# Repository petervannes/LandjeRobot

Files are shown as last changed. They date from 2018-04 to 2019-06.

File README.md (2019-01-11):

# Landje Robot

cover

Welcome to the Landje Robot repository. Landje Robot is an fully open source STEM robot and named after the elementary school of my kids where i started teaching programming using this robot. It is a common object avoidance and line following robot like many others. Landje Robot deviates in two aspects from many other builds.

First, Landje Robot is fully documented. There is a [Preparation guide](https://petervannes.github.io/LandjeRobot/Landje%20robot%20Kit%20preparation.html) which describes the bill of material, assembly of wire looms and other main parts and designs of the 3D printed parts. Next to the [Preparation guide](https://petervannes.github.io/LandjeRobot/Landje%20robot%20Kit%20preparation.html) there is a [Student guide](https://petervannes.github.io/LandjeRobot/Student%20guide%20ENU.html) with programming lessons in [English](https://petervannes.github.io/LandjeRobot/Student%20guide%20ENU.html) and [Dutch](https://petervannes.github.io/LandjeRobot/Student%20guide%20NLD.html).

Secondly, Landje Robot has its own instruction set. The instruction set is also documented in [Dutch](https://petervannes.github.io/LandjeRobot/instructionset%20NLD.html) and [English](https://petervannes.github.io/LandjeRobot/instructionset%20ENU.html). This instructionset simplifies the control of the sensors, motors, led and switch. With this instruction set and robot i made an attempt to create instruction material for kids who have overgrown the level of programming in Scratch or similar languages like Blockly and Alice. Programming in Scratch is a good starting point to grab the concepts of programming, but it has it's limitiations. (as this robot has it's own)

Switching from the safe Scratch language to C is challenging with it syntax and runtime errors. Therefore the complexity of controlling the I/O ports to read sensor data or control the servo- and stepper motors is delegated to the provide instructionset. Moving the robot forward is now reduced to a `move ( direction )` instruction.

For documentation and components there has been made use of open source components and products as much as possible. Documentation is written in MarkDown or HTML format. Graphical content is made using [GIMP](https://www.gimp.org) for bitmaps and [Inkscape](https://inkscape.org/en/) for vector oriented images.

All documentation is clearly published [here](https://petervannes.github.io/LandjeRobot/)

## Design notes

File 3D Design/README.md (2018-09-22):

# Landje ROBOT 3D Printer Parts

The Landje robot is made up of various 3d printed parts.
You can download the stl-files for the different parts directly from the [LandjeRobot](https://github.com/petervannes/LandjeRobot/tree/master/3D%20Design) GitHub repository.

The parts shown on the [blog](http://reddipped.com) or in the guides are printed on a Ultimaker 3 using original Ultimaker PLA and PVA filament for best results. Optimal UM3 Profile settings for printing these parts are available in the folder [/3D Design/UM3](https://github.com/petervannes/LandjeRobot/tree/master/3D%20Design/UM3).

You can always change the model to your needs. The original design is available on [TinkerCad](https://www.tinkercad.com/things/dualnxm5zyQ-landje-robot).

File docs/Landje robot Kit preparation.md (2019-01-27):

# Landje robot Kit preparation

[TOC]

## Introduction

This guide documents the parts and tools to be purchased to create a complete Landje robot kit.
Part of the preparation is assembling the wiring looms and preparation of the led and its wiring.
If you have completed this guide the kit will reassemble the picture below. 



## Part list

### Hardware

|Qty|Article|Details|Est.&nbsp;&nbsp;price|
|:---|:---|:---|:--|
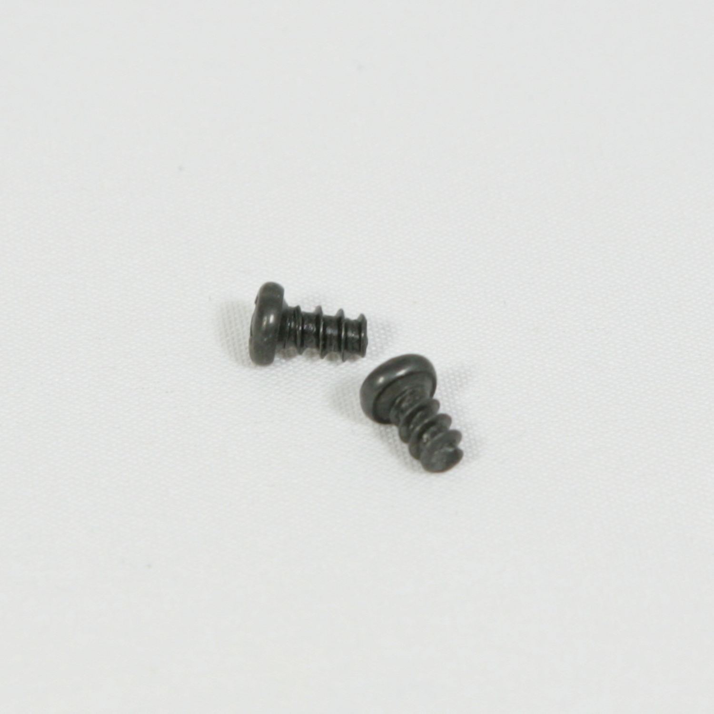
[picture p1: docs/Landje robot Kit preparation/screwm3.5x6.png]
|4| Philips head self-tapping micro screws. M3.5x6|[ AliExpress](https://nl.aliexpress.com/item/100Pcs-M2-6-M3-M3-5-M4-PB-Phillips-Head-Micro-Screws-Round-Head-Self-tapping/32818885586.html)|€ 0,13|
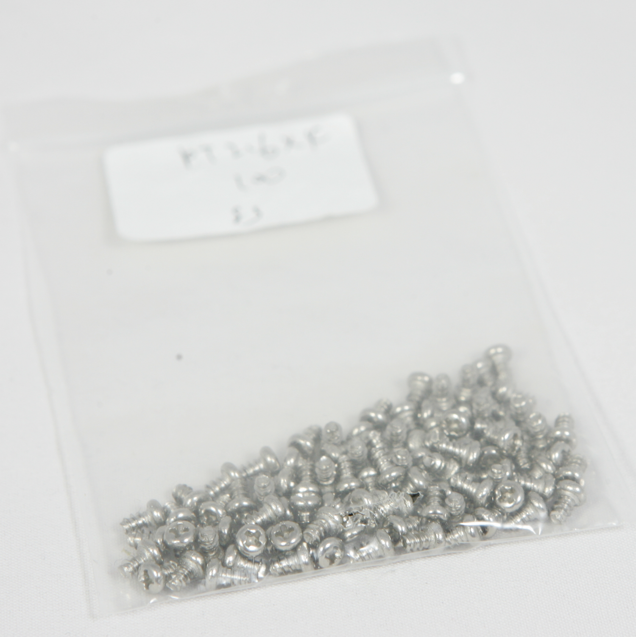
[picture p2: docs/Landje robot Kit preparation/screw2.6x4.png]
|10| Philips head self-tapping micro screws. M2.6x4 |  [AliExpress](https://nl.aliexpress.com/item/100pcs-lot-M2-M2-3-M2-6-M3-Stainless-steel-pan-head-philips-cut-off-tail/32811488462.html)|€ 0,28|
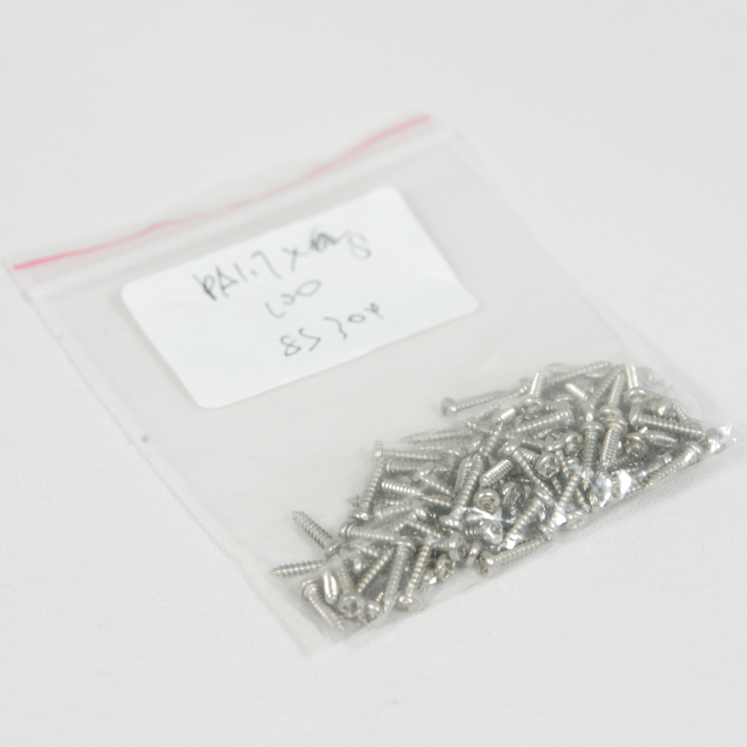
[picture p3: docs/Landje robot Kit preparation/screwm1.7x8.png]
|4| Philips head self-tapping micro screws. M1.7x8 |  [AliExpress](https://nl.aliexpress.com/item/100pcs-lot-M1-M1-2-M1-4-M1-5-M1-6-M1-7-Stainless-steel-phillips/32805873422.html)|€ 0,14|
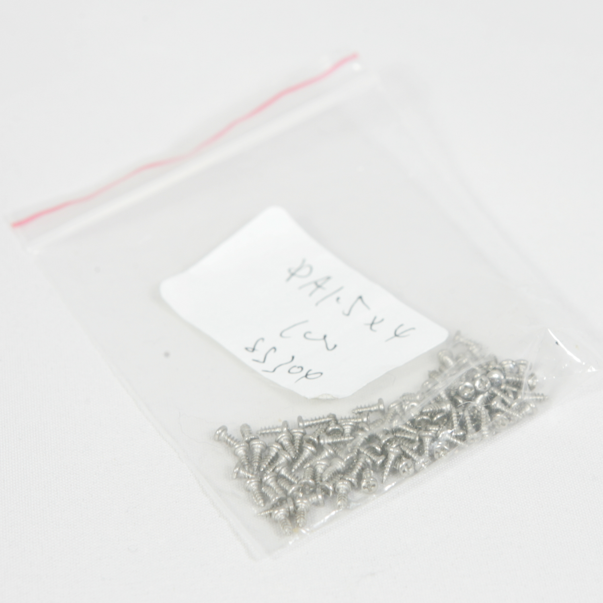
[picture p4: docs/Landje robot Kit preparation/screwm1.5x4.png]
|4| !!!!!!!!!!!!!!!! CORRECION Philips head self-tapping micro screws. M1.7x4 |  [AliExpress](https://nl.aliexpress.com/item/80pcs-M2-Phillips-head-micro-screws-round-head-self-tapping-electronic-small-screws-Black-zinc-Hard/32596628894.html)|€ 0,12|

### Electronics 

|Qty|Article|Details|Est.&nbsp;&nbsp;price|
|:---|:---|:---|-----:|
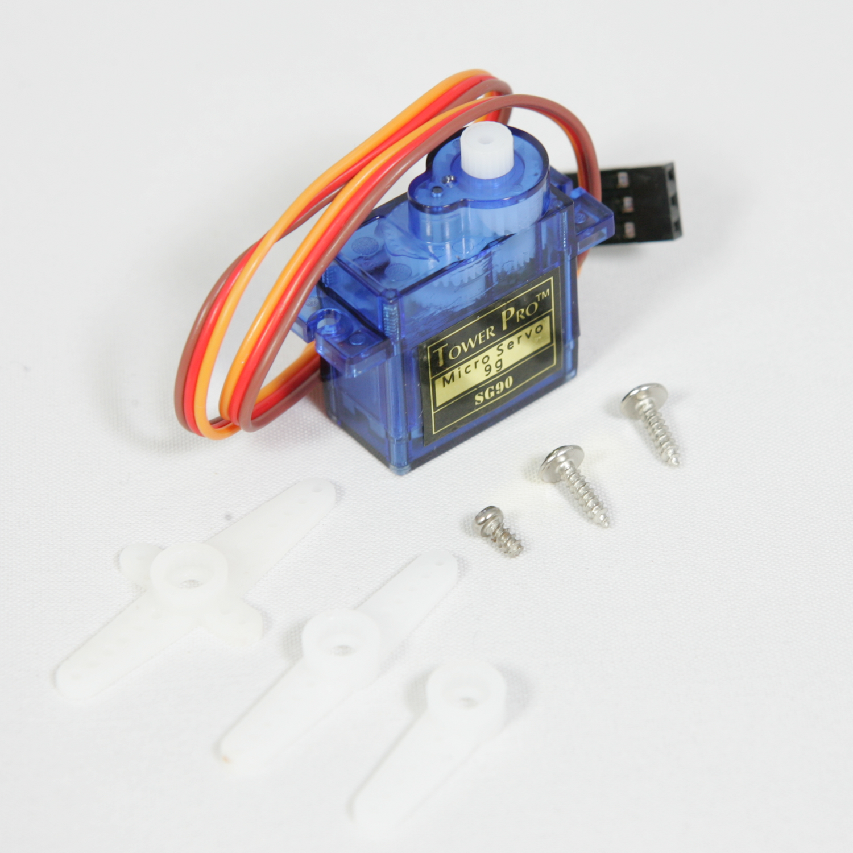
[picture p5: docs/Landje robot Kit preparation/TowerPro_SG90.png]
|1|Tower pro SG90 RC Micro Servo 9g |  [AliExpress](https://nl.aliexpress.com/wholesale?catId=0&initiative_id=SB_20171217044656&SearchText=sg90+micro+servo)|€ 1.05|
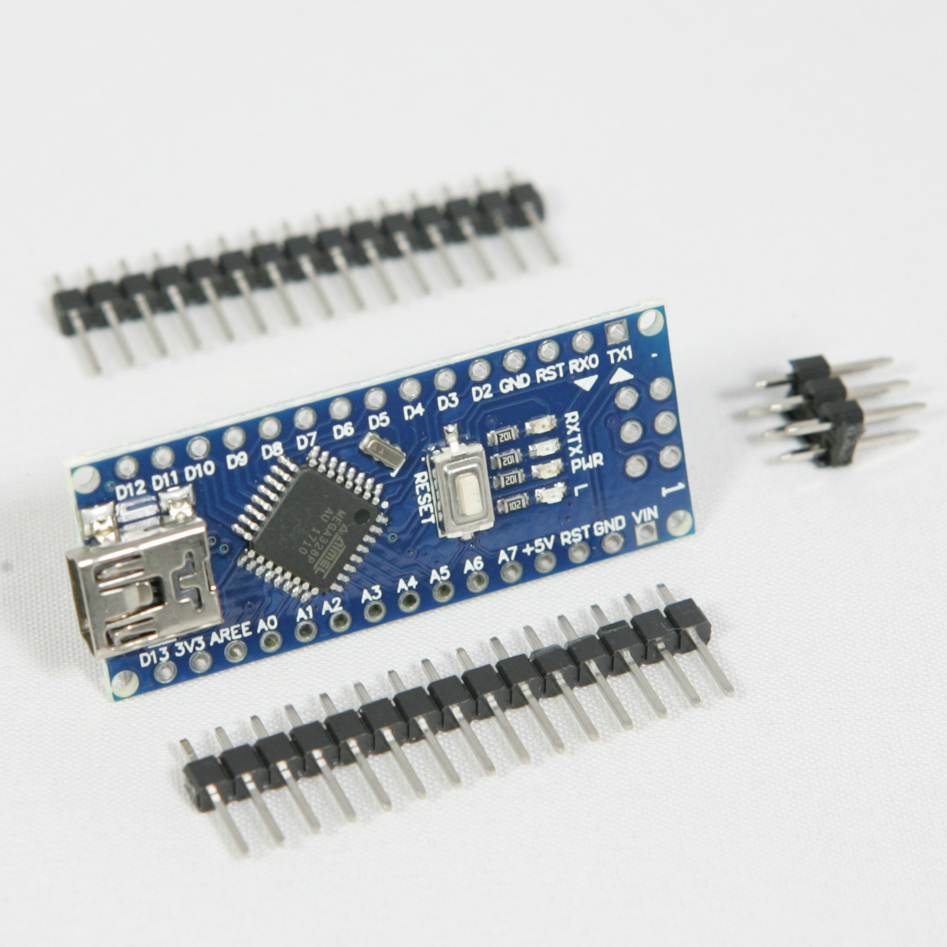
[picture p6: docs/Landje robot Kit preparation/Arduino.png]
|1|Arduino Nano 3.0</br> CH340 USB driver 16 Mhz|  [AliExpress](https://nl.aliexpress.com/w/wholesale-arduino-nano-ch340-usb-driver.html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)| € 2,00|
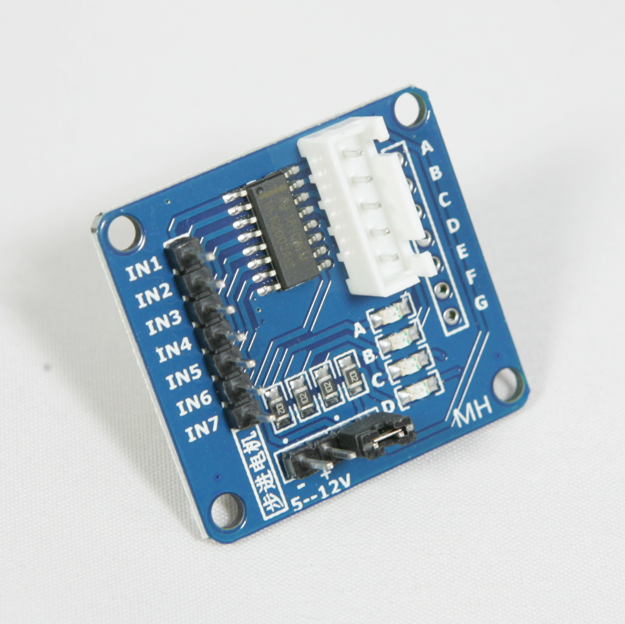
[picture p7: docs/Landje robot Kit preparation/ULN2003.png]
| 2 | ULN2003 Stepper Motor Driver Board SMD | [AliExpress](https://nl.aliexpress.com/item/High-power-ULN2003-Stepper-Motor-Driver-Board-Test-Module-For-Arduino-AVR-SMD/32561202872.html) | € 1,16 |
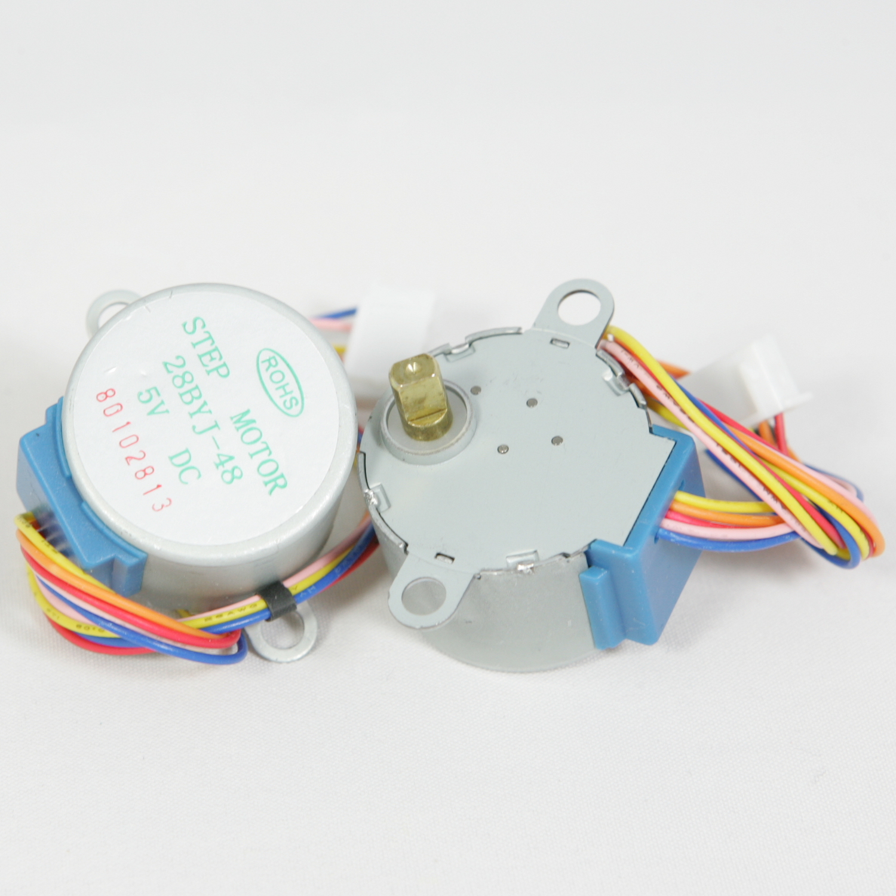
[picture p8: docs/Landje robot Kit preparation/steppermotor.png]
| 2 | 28BYJ-48-5V Stepper motors | [AliExpress](https://nl.aliexpress.com/item/LIXF-2017-HOT-New-38g-Silver-Plastic-28BYJ-48-5V-4-Phase-5-Wire-DC-5V/32827355981.html) | € 2,28 | 
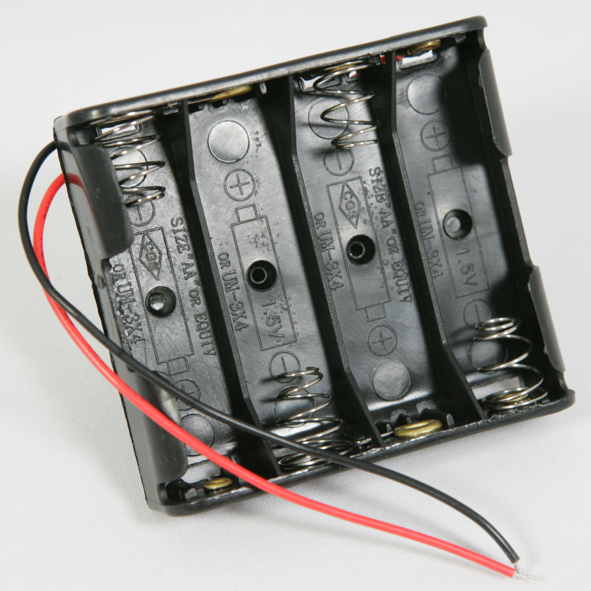
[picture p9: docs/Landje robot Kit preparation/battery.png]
| 1 | AA Power Battery Storage</br> Case Plastic Box Holder With 4 Slots | [AliExpress](https://nl.aliexpress.com/item/Top-Quality-Hot-Sale-1pcs-AA-Power-Battery-Storage-Case-Plastic-Box-Holder-With-4-Slots/32685809303.html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) | € 0,40|
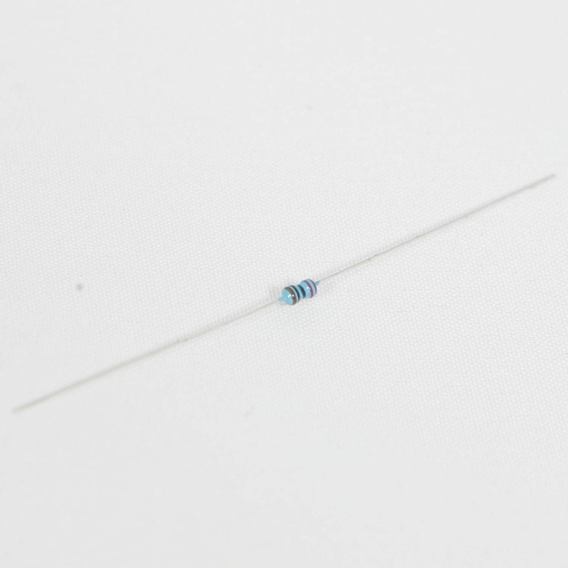
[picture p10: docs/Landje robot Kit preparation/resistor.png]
| 1 | 1/6W Metal Film Resistor 220Ω | [AliExpress](https://nl.aliexpress.com/item/100pcs-1-6W-Metal-Film-Resistor-220-ohm-220-R-1-Tolerance-Precision-RoHS-Lead-Free/1852424272.html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) | € 0,01 |
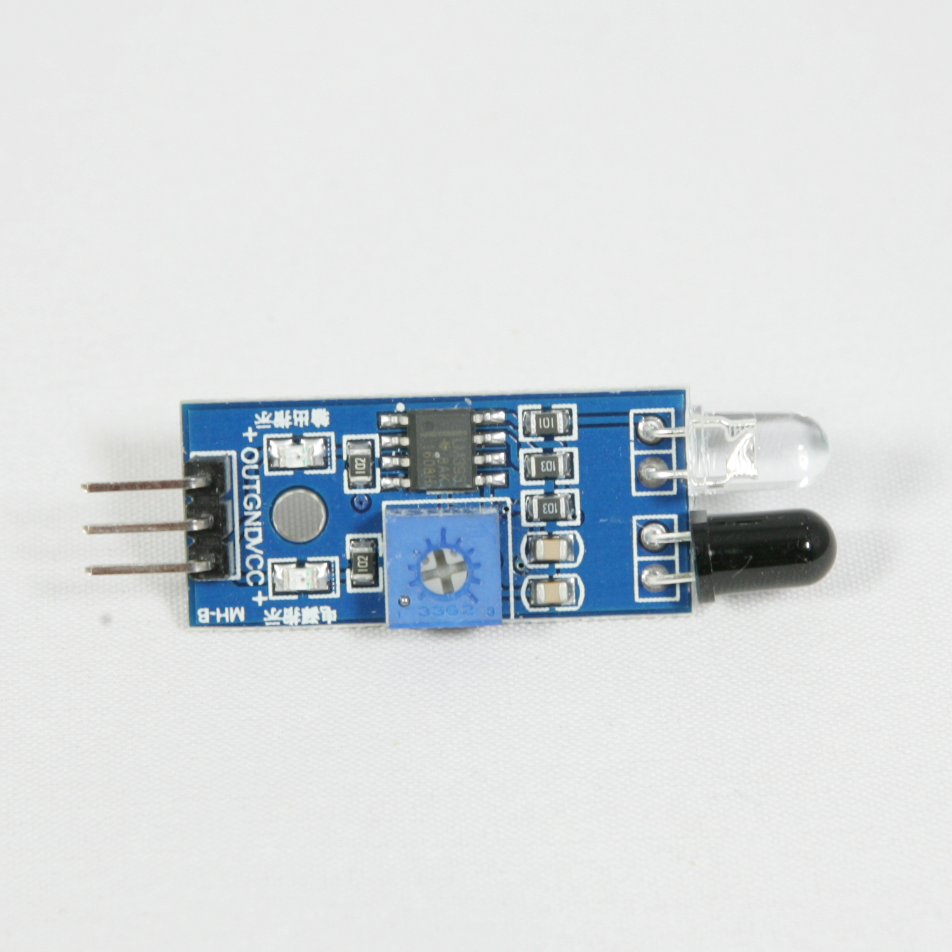
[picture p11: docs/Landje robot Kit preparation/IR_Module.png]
| 2 | IR Infrared Obstacle Avoidance Sensor Module | [AliExpress](https://nl.aliexpress.com/item/IR-Infrared-Obstacle-Avoidance-Sensor-Module-for-Arduino-Smart-Car-Robot-3-wire-Reflective-Photoelectric/32340011898.html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) | € 0,90 |
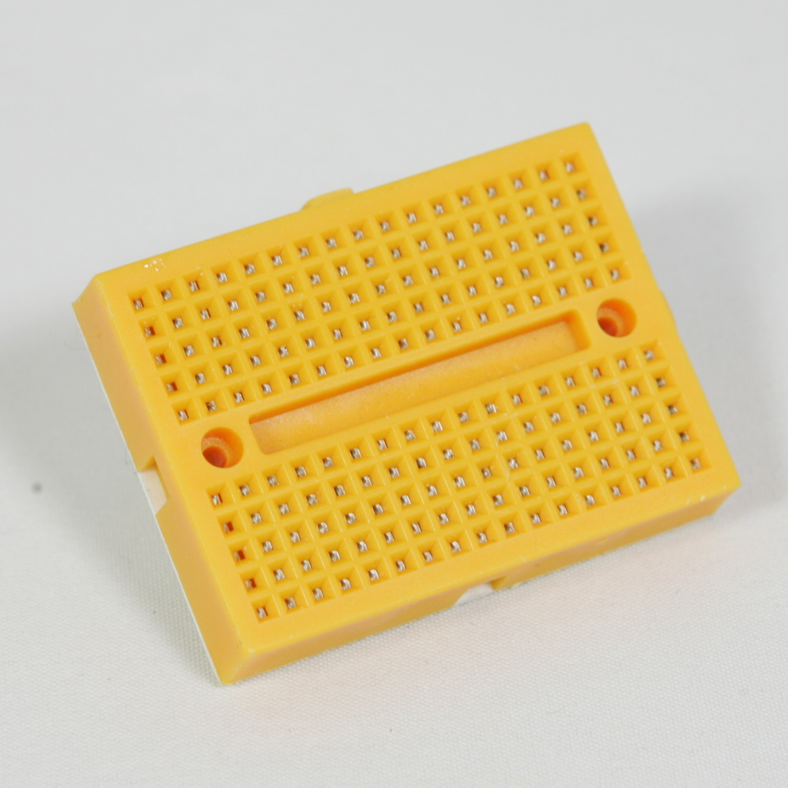
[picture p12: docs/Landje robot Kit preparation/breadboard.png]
| 1 | SYB-170 Mini Solderless Prototype Breadboard | [AliExpress](https://nl.aliexpress.com/item/3pcs-lot-170-Tie-points-Mini-Solderless-Prototype-Breadboard-for-ATMEGA-PIC-Arduino-UNO-Wholesale-Retail/1536996696.html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) | € 0,45 |
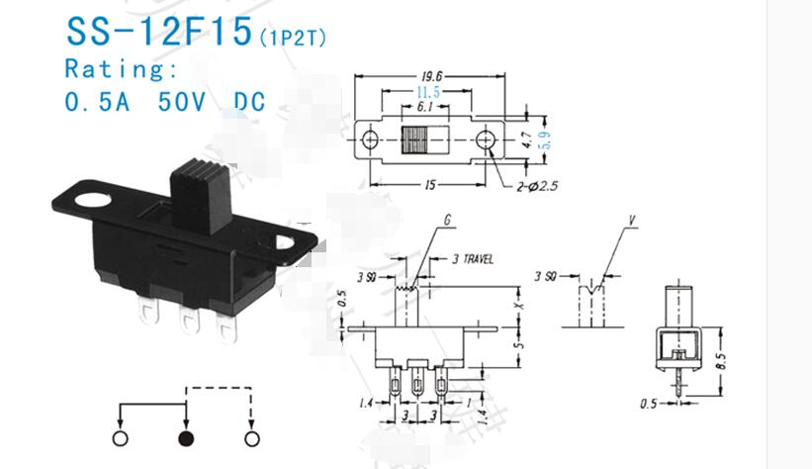
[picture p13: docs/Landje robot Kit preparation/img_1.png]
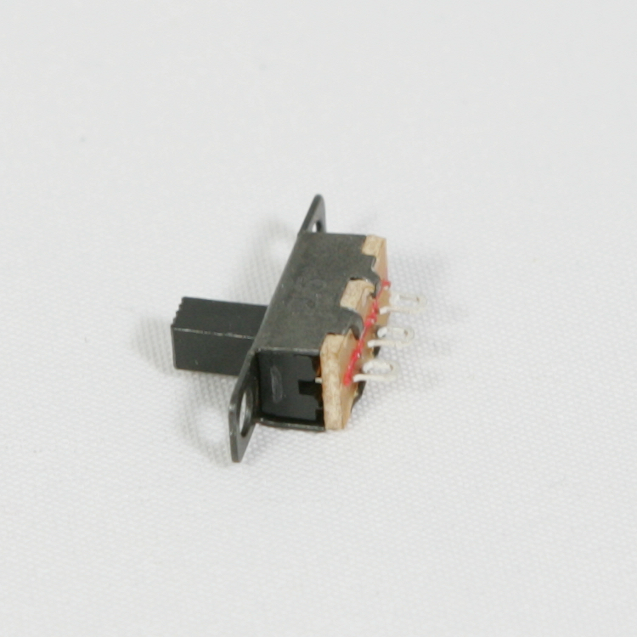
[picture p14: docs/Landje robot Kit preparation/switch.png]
| 2 | 5mm Height Knob 3 Pin 2 Position</br> 1P2T SPDT Panel Slide Switch 0.5A | </br>[AliExpress](https://nl.aliexpress.com/item/50-Pcs-5mm-Height-Knob-3-Pin-2-Position-1P2T-SPDT-Panel-Slide-Switch-0-5A/32706649448.html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) | € 0,16|
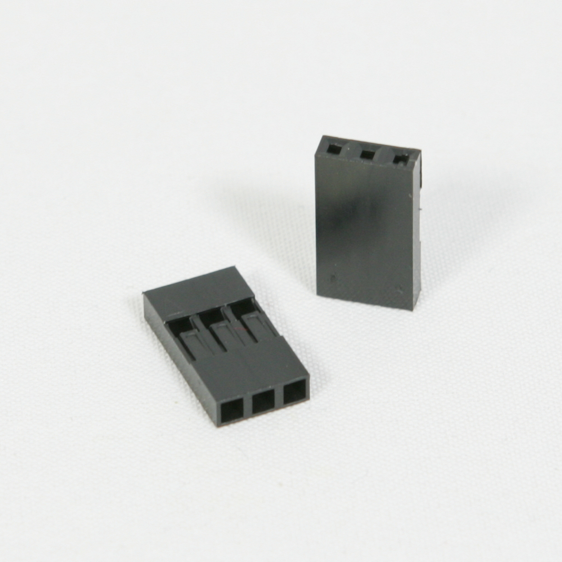
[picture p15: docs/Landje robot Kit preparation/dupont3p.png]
| 2 | Dupont connector 3 pin single row 2.54 mm | [AliExpress](https://nl.aliexpress.com/item/For-dupont-connector-6pin-single-row-2-54mm-for-dupont-plastic-shell-through-hole-100pcs-lot/32637991458.html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) | € 0,03 |
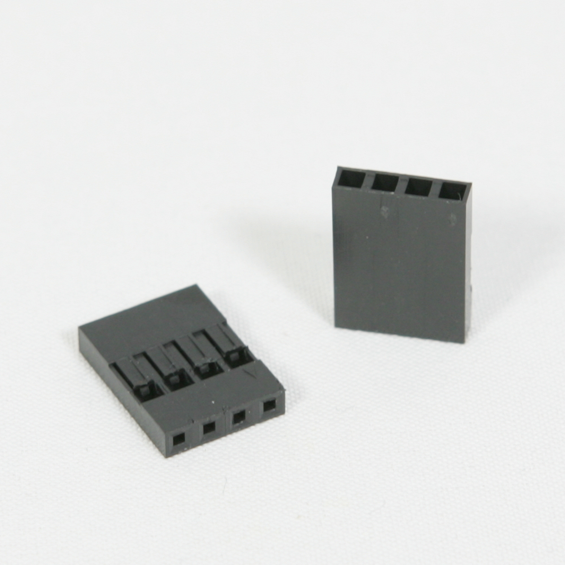
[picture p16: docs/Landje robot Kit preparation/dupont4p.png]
| 5 | Dupont connector 4 pin single row 2.54 mm | [AliExpress](https://nl.aliexpress.com/item/For-dupont-connector-6pin-single-row-2-54mm-for-dupont-plastic-shell-through-hole-100pcs-lot/32637991458.html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) | € 0,08 |
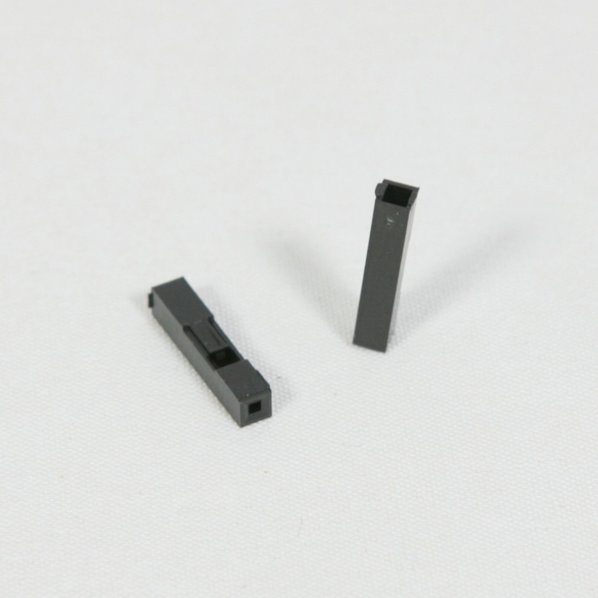
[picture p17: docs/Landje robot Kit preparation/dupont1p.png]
| 26 | Dupont connector 1 pin single row 2.54 mm  | [AliExpress](https://nl.aliexpress.com/item/For-dupont-connector-6pin-single-row-2-54mm-for-dupont-plastic-shell-through-hole-100pcs-lot/32637991458.html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) | € 0,31 |
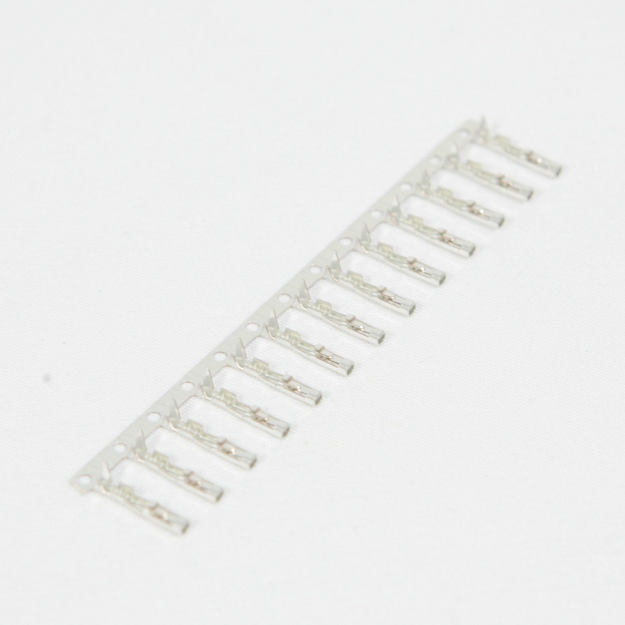
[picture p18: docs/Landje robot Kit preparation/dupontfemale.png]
| 22 | Dupont connector reed 2.54 mm metal terminal female | [AliExpress](https://nl.aliexpress.com/item/For-dupont-reed-tinniness-copper-2-54mm-for-dupont-indeneter-s-terminal-femal-100pcs-lot-free/32637923845.html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) | € 0,30 |
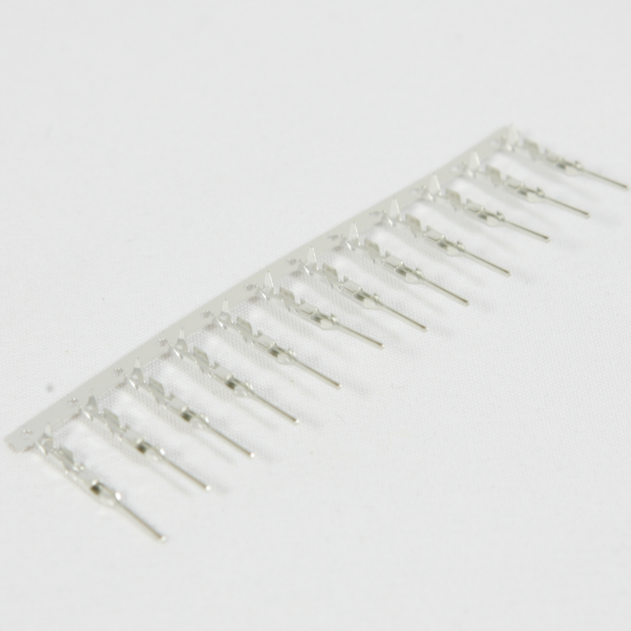
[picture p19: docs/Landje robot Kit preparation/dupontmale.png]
| 29 | Dupont connector reed 2.54 mm metal terminal male | [AliExpress](https://nl.aliexpress.com/item/For-dupont-reed-tinniness-copper-2-54mm-for-dupont-indeneter-s-terminal-femal-100pcs-lot-free/32637923845.html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) | € 0,50 |
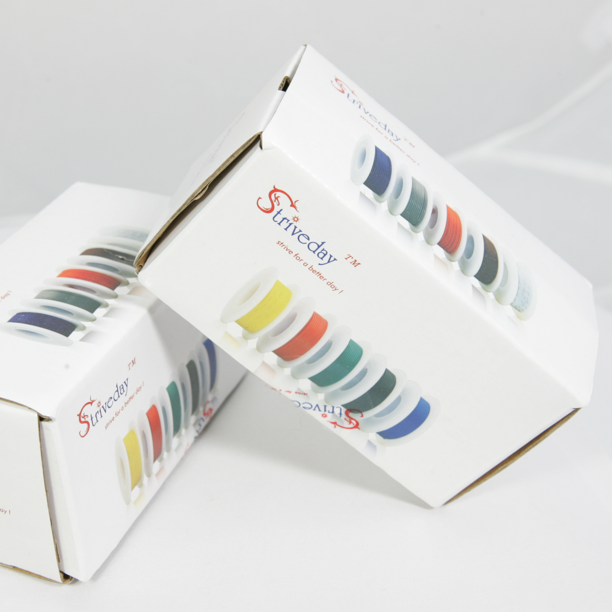
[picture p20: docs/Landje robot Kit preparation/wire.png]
| 6 | Different colors of 26AWG Silicone Wire</br>Red, Black, Blue, Green, Yellow, Purple | Buy 2 boxes of Striveday 26AWG Silicone Wire.</br> Sufficient to build a colony of robots</br>Each robot requires about 1.5m wire.</br></br>[AliExpress](https://nl.aliexpress.com/item/50-Meters-30AWG-Silicone-Wire-5-color-Mix-box-1-box-2-package-Electrical-Wire-Line/32795667621.html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) | € 0,50|
| 1 | Ultrasonic Module HC-SR04</br>Distance Measuring Transducer Sensor| [AliExpress](https://nl.aliexpress.com/item/Ultrasonic-Module-HC-SR04-Distance-Measuring-Transducer-Sensor-HC-SR04-HCSR04-ultrasonic-transducer-ultrasonic-sensor/32319720974.html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)| € 0,80|
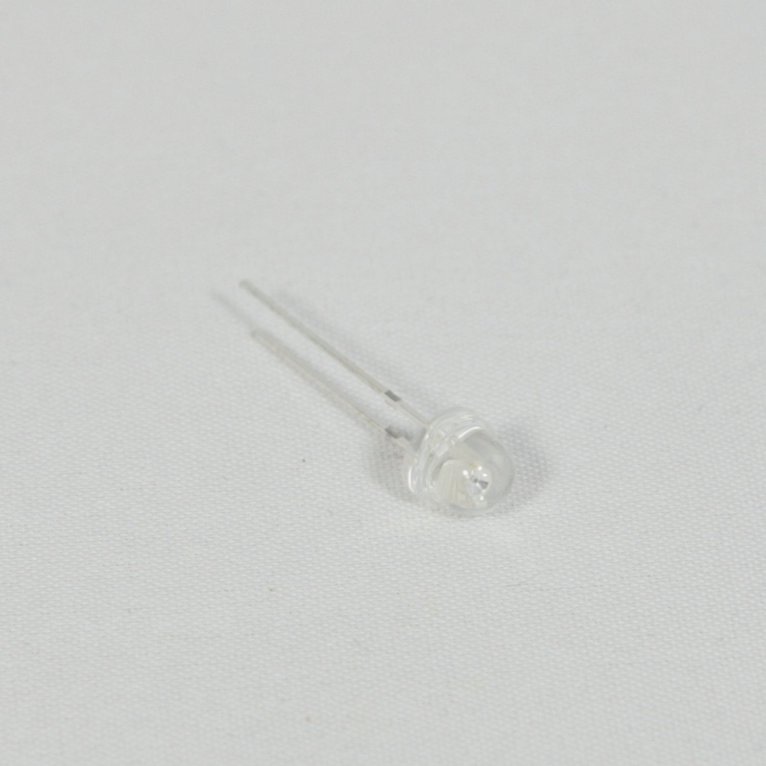
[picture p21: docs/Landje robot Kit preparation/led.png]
| 1 | 5mm(4.8mm) Red straw hat LED | [AliExpress](https://nl.aliexpress.com/item/Free-shipping-100PCS-LOT-5mm-4-8mm-Pure-RED-straw-hat-LED-lamp-beads-super-bright/32574474990.html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) | € 0,02 |
| 1 | USB Cable

### Miscelleanous parts

|Qty|Article|Details|Est.&nbsp;&nbsp;price|
|:---|:---|:---|-----:|
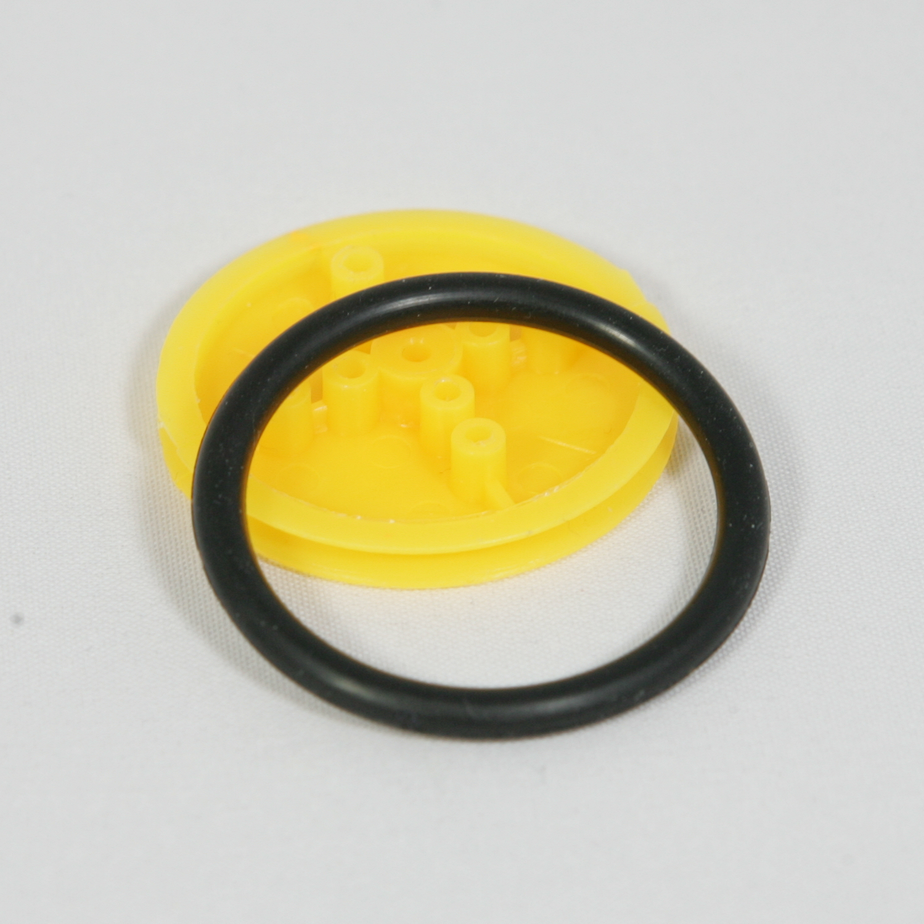
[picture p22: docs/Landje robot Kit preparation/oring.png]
|2| O-Ring 36mm | Buy some Plastic Robot Chassis Wheels with Rubber Band and discard the wheel.</br> </br>[AliExpress](https://nl.aliexpress.com/item/20pcs-lot-Small-Smart-Car-Tire-Chassis-Plastic-Robot-Chassis-Wheel-Free-Shipping/32604695447.html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)|€ 0,59|
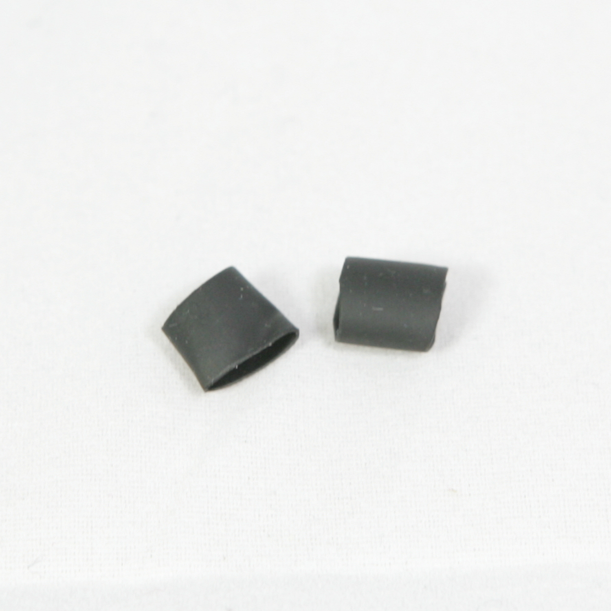
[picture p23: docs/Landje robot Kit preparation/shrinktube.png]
| 1| 2cm length 4MM heat shrink tube|  [AliExpress](https://nl.aliexpress.com/item/20meters-lot-4MM-Heat-Shrink-Tubes-Shrinkable-Tubing-Insulation-Sleeving/1682188162.html)| € 0,01|
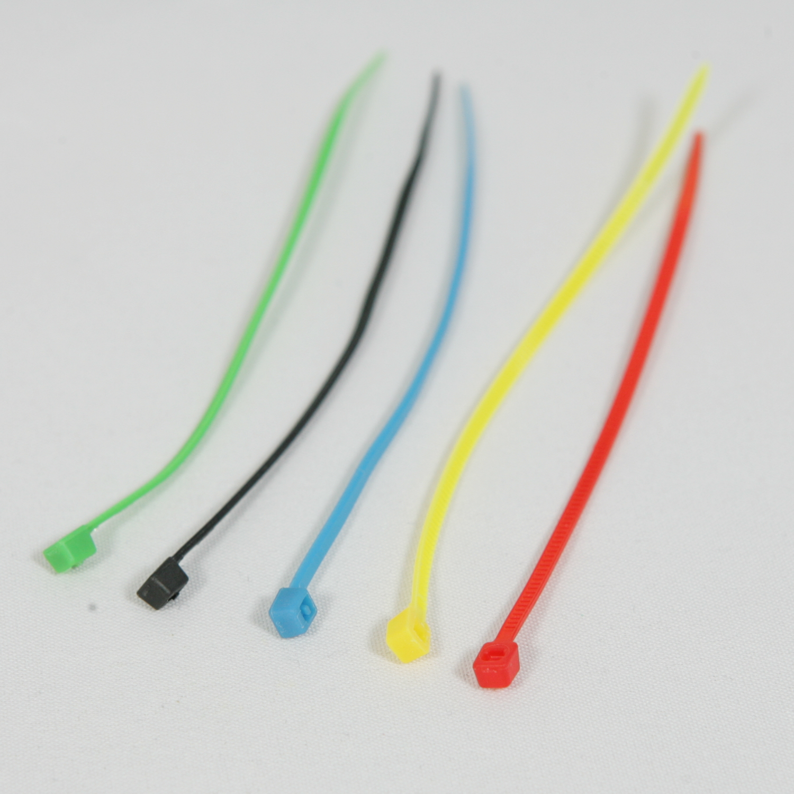
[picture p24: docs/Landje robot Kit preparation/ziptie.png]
| 8 | 100mm x 2mm wire zip ties | </br>[AliExpress](https://nl.aliexpress.com/item/High-quality-900pcs-box-Self-Locking-100mm-X-2mm-Brand-New-Nylon-Cable-Wire-Zip-Ties/32697081164.html)| € 0,11|
| 1 | 12mmx2mm Stainless Steel Round Rod Axle Bars for RC Toys | </br>[AliExpress](https://nl.aliexpress.com/item/JFBL-Hot-20PCS-170mm-x-2mm-Stainless-Steel-Round-Rod-Axle-Bars-for-RC-Toys/32824449469.html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)| € 0,01|

### 3D printed parts

I developed the 3D printed parts using Tinkercad and an Ultimaker 3 printer. Because results of the printed parts may slightly differ per printer and the used parts may change over time you may need to adopt the design of the parts. Therefore the designs are freely available on Tinkercad in the project [TinkercadProjectName](http://some). The STL files can be directly downloaded from the [STL](https://github.com/reddipped/LandjeRobot/tree/master/3D%20Design/STL) folder in the Github repository. An optimal Curaprofile can be dowloaded also from the [UM3](https://github.com/reddipped/LandjeRobot/tree/master/3D%20Design/UM3) folder when printing on an UM3 with PLA and PVA as support material. 

|Qty|Article|Details|Est.&nbsp;&nbsp;price|
|:---|:---|:---|-----:|
|1| Frame|  </br>Requires about 77g PLA and 86g PVA |€ 16,03|
| 1| Head| </br>Requires about 14g PLA and 13g PVA| € 2,69|
| 2 | Wheel | </br>Requires about 6g PLA and 2g PVA| € 0,72|
| 1 | Tail wheel | </br>Requires about <1g PLA and 0g PVA| € 0,07|
| 1 | Tail wheel steering arm | Requires about <1g PLA and 0g PVA| € 0,07|
| 1 | Screw organizer | </br>Requires about 3g PLA and 0g PVA| € 0,24|

### Tools

|Qty|Article|Details|Est.&nbsp;&nbsp;price|
|:---|:---|:---|-----:|
|1| PH00 1.5 |  Philips PH00 1.5 screwdriver |€ |
|1| PH1 |  Philips PH1 screwdriver |€ |

## Assembly tools

For the kit preparation some more and some less general available tools are required

* A small side cutter
* A heavy duty side cutter
* A pair of small straight pliers
* Solder station 
* Tin/Lead 40/60 solder
* 3D Printer

# Kit preparation instructions

## Cables

In the next images all wiring looms which need to be assembled are documented.
I do personally have bad experience with Dupont crimping pliers and prefer to solder to wires to the Dupont connectors.
Soldering, although it requires a steady hand, is not heard and needs a little bit of practice.

### Soldering Dupont wires

Cut of the fold-over wings    

</br>

Strip the cable-end about 2mm and tin it    
</br>

Tin the Dupont connector    
</br>

Solder the wire to the connector.    

</br>

Fold the wings over the wire using a combination or radio plier    

</br>

### Wiring loom set

Create the wiring looms shown below. Please be aware that the images may not scale right. If you want to print them on the right scale, download the file [wiring diagram.svg](https://github.com/reddipped/LandjeRobot/blob/master/Guides/Landje%20robot%20Kit%20preparation/wiring%20diagram.svg) and use Inkscape to open and print the file without borders (no-slug). Alternatively you can download the "wiring diagram_*.png" files from the [Landje robot Kit preparation](https://github.com/reddipped/LandjeRobot/tree/master/Guides/Landje%20robot%20Kit%20preparation) folder and print the files border-less (no-slug) on A4 paper. 

**Servo wires**
Servos by default have a 3-pin female dupont connector. Cut the servo cable to the desired length and replace the 3-pin female dupont connector by 3 1-pin male dupont 







## Robo head

Depending on the (motoric) skills of the students, you can prepare the robot head or let the students assemble and solder the parts themselves. For 8th grade primary school students i did the preparation. 

### Parts 
First gather the necessary parts to assemble the robot head.

* 1/6w metal filmm resistor 220Ω
* HC-SR04
* 5mm Led
* 2 wire zip ties
* 3d printed head
* Led Anode wire
* HC-SR04 wiring loom

### Assembly

Hold the 3d printed head so the back faces towards you. 
Push the resistor in the outer brackets.</br>
 

Bend both end of the resistor wires 90º and push the wires in the center brackets.</br>
 

Bend the right wire of the resistor 90º and push it in the right middle bracket.</br>
 

Place the led into the recess. Make sure the kathode, the shorter pin, is on your left. Push the led into the recess of the mouth until it clicks. If you need to apply to much pressure, slightly warm the head using a hot airgun. Make sure no to heat it to much to prevent deformation. When printed in PLA a temperature of 35 degrees is sufficient to soften  the plastic.</br>
 

Take the led bend both wires 90º, then make two bends 90º in the left wire till it connects to the resistor. Make three 90º bends in the right wire until it can be pushed into the last unused bracket. </br>
 

Solder the kathode of the led to the resistor lead and the blue 80mm wire to the anode.</br>
 

Take the HC-SR04 loom and solder the black lead without the dupont connector to the other lead of the resistor.</br>  
 

Push the HC-SR03 ultrasonic sensor gently into the socket until it clicks</br>
 

Fasten the black and red wire on the left by threading a cable-ties through an eyelet and fastening it. Repeat the process for the other side for the blue and yellow wire.</br>
 

Cut of the leads of the cable-ties and the assembly of the head is finished.</br>
 
 

## IR Sensor module

The IR Sensor module has an IR light emitter and receiver. Depending on the print material and colour of the frame it may more or less conduct the IR light shine through. When conducting to much light the sensor will not able detect lines. Therefore a piece of 6mm black heat shrink tube has to be put on the IT light emitter.

Slide the heat shrink tube ove rthe IR light emitter. The emitter led is the translucent led.</br>
 
 

Carefully head the shrink tube, making sure the other compontents do not get overheated. The heat shrink tube must be tight enough so you cannot slide it of the led after it has been cooled down </br>
 

## Tail wheel

To assemble the tail wheel, cut a piece of 12mm from the 2mm Stainless Steel Round Rod.</br>
 

Place the wheel in the boom so the axle of the wheel is aligned with the holes in the boom. Push the rod through a hole in one side of the boom. </br>
 

Gently push the rod untill it comes out of the hole on the other side of the boom.</br>
 

## servo wiring

Due to a aberrant connector layout on the ULN2003 stepper motor driver boards the wiring on the stepper motor drivers have to be adapted to match the correct pins on the ULN2003.

All stepper motors i have received have the following wiring configuration. With the stepper motor axis and connector side with the 2 notches facing towards you the pins are labeled 1 to 5 when counting from left to right. 

On the image below the wires for a new received stepper motor are wired as follows.

stepper 1 (coil 1) to connector 3  
stepper 2 (coil 3) to connector 1  
stepper 3 (+5v) to connector 2  
stepper 4 (coil 4) to connector 4  
stepper 5 (coil 2) to connector 5  

Note that the connector on the photo below is turned.

 

To rewire the connector, remove the wires from the connector first. I have tried different tools to removed the pins from the connector and got the best results using a T3 screwdriver bit.

Place the connector on a flat surface with the five cutouts facing upwards. Gently push the little notch, which keeps the connector in place, down,
 

and pull the cable outside the connector at the same time. 

 

Repeat this step for all wires.

 

Now place the wires into the connector again, one by one.

stepper 1 (coil 1) to connector 2  
stepper 2 (coil 3) to connector 1  
stepper 3 (+5v) to connector 5  
stepper 4 (coil 4) to connector 3  
stepper 5 (coil 2) to connector 4  

(Yes! the wire on the picture below is not positioned correctly 😃)

 

And after completion the wiring should match the image below. Ignore the colour of the wires when comparing your stepper motor wiring with the photo below. Different stepper motor suppliers do use different wire colours and ordering of colours. Only compare the order of the wires from the stepper motor.

 

## Arduino create preparation school accounts

When using [Arduino Create](https://create.arduino.cc) and Chromebooks an Arduino Create subscription is required. There are two plans available for Arduino Create, a personal plan and an educational plan.

### Personal plan
When you want to subscribe yourself to Arduino Create, visit the Chrome web store and take a monthly subscription on Arduino Create [here]( 
https://chrome.google.com/webstore/detail/arduino-create/dcgicpihgkmccjigalccipmjlnjopdfe)

### Educational plan
If you are in an educational environment, you should use the [Arduino Create App for Education](https://create.arduino.cc/plans/chrome-app). A detailed description how to subscribe to subscribe to the Arduino Chrome App for Education can be found [here](https://create.arduino.cc/projecthub/Arduino_Genuino/how-to-subscribe-to-the-arduino-chrome-app-for-education-6ae9c8). 

Follow the instructions to create a team and add the students to the plan. If the students have been added successfully, the Arduino Create for Education Chrome app can be installed by following the steps in the [Install Arduino Create for Education Chrome app](https://create.arduino.cc/projecthub/Arduino_Genuino/install-arduino-create-for-education-chrome-app-6bf22a) article.

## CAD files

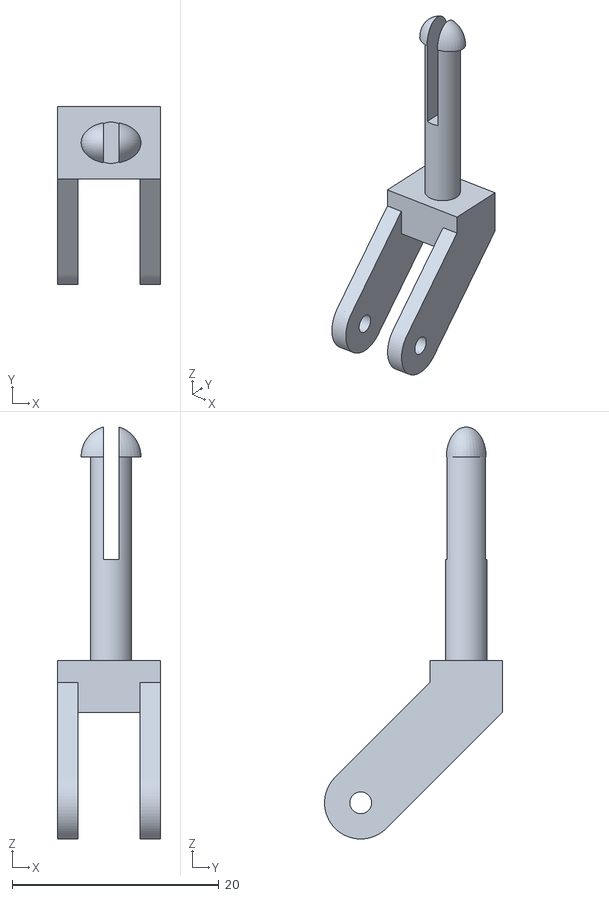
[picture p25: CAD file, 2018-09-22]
3D Design/STL/robot tail wheel steering arm .stl
10.0 x 17.2 x 39.8

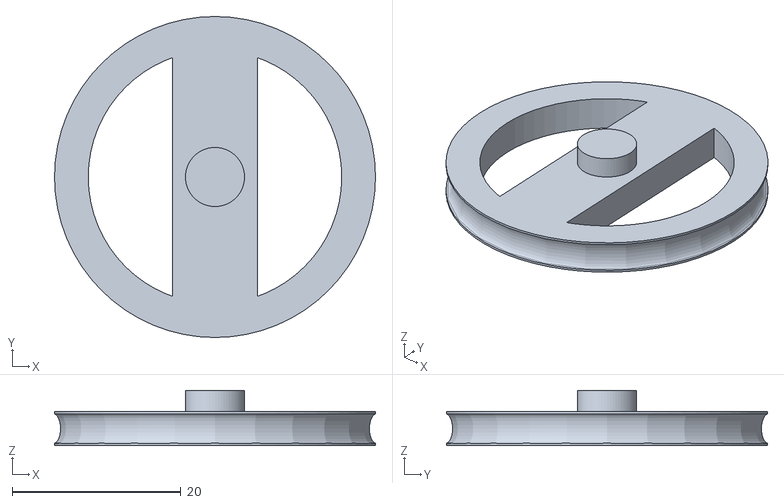
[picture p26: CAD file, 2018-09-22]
3D Design/STL/robot wheel.stl
38.0 x 38.0 x 6.51

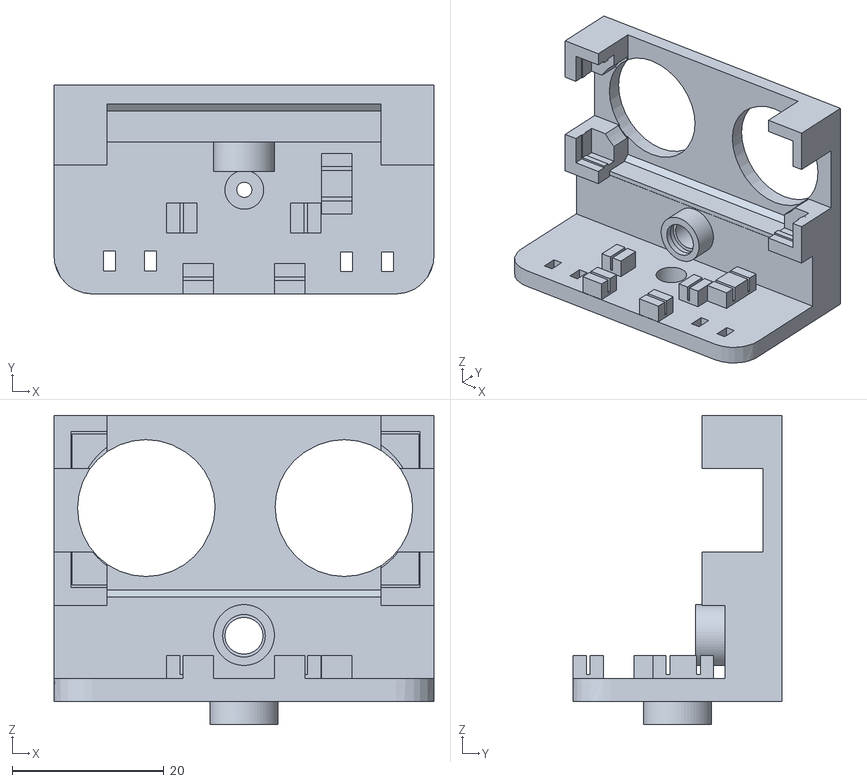
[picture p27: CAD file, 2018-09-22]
3D Design/STL/Landje Robot.stl
50.0 x 27.5 x 40.7

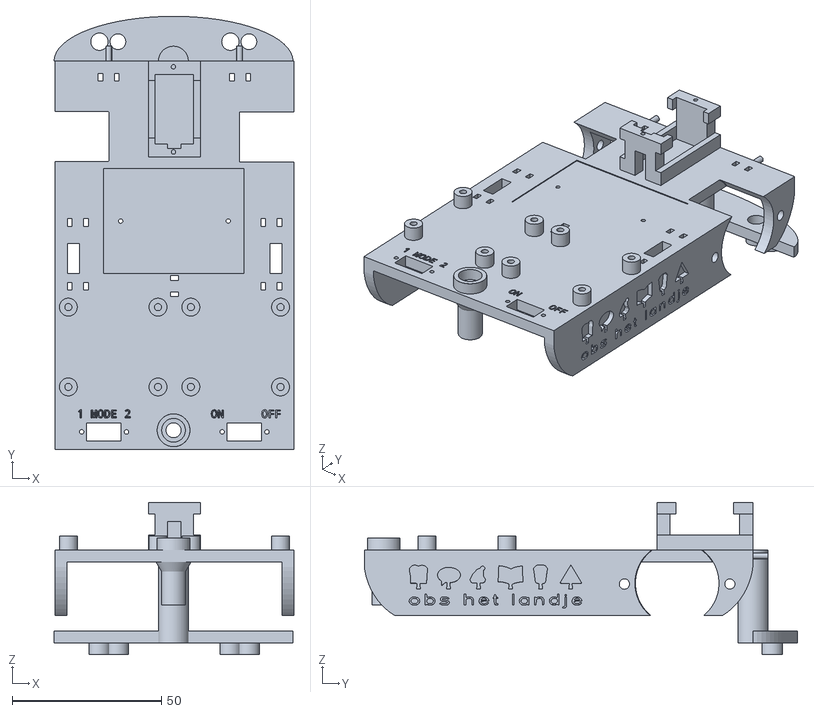
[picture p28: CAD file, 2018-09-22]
3D Design/STL/robot frame.stl
80.3 x 145.0 x 51.0

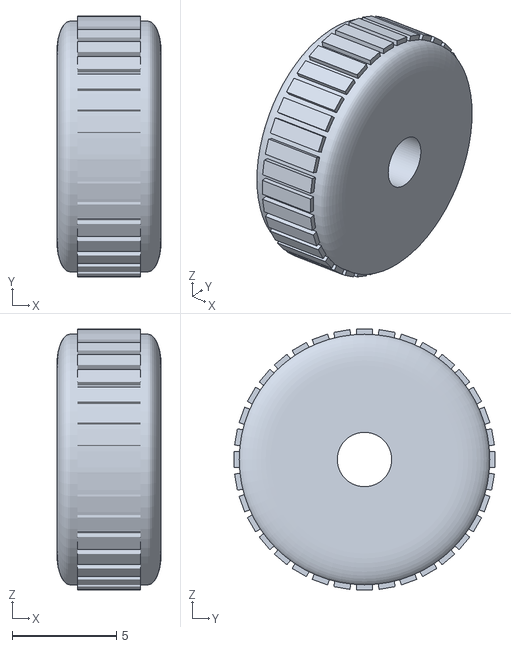
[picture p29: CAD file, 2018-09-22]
3D Design/STL/robot tail wheel.stl
5.00 x 12.5 x 12.5

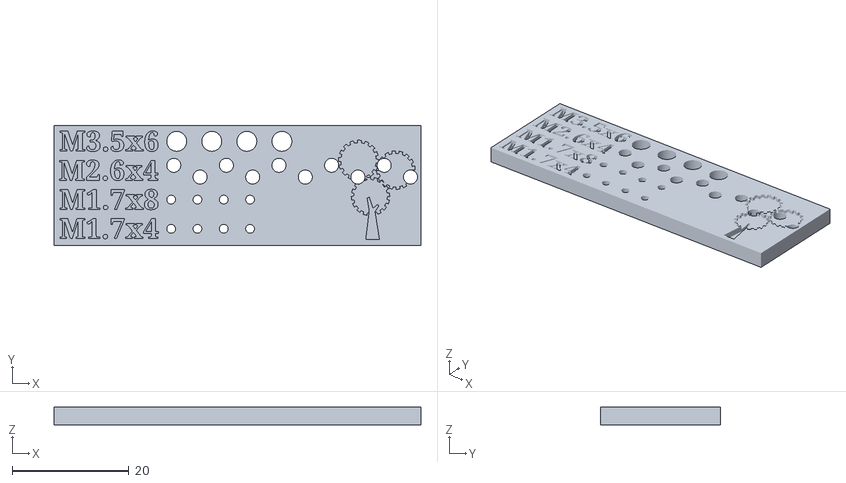
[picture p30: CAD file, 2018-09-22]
3D Design/STL/robot screw organizer.stl
62.8 x 20.5 x 3.00

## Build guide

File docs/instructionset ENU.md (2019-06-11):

# Landje Robot Instructionset

The Landje robot has its own instruction set. With these instructions you can easily control the robot.

Every program for a Landje Robot must start with the following instructions. You do not need to understand these instructions, just copy and paste these instructions when you start a new program. 

```
#include <LandjeRobot.h>

// Robot motor connections
const int motor[2][4] = {
  {2, 3, 4, 5}, {6, 7, 8, 9}
};

// Line sensor connections
const int lineSensors[2] = { 10, 11 };
// Light floor with dark lines = true
// Dark floor with light lines = false 
const bool lineSensorInverse = true;

// Wheel circumference in cm
const int wheelRadiusMM = 21;
// Track width in cm
const int trackWidthMM = 98;

// Ultrasonic sensor connections
int ultraPin = 13;

// Servo connections
int servoPin = 14;

// Led connection
int mouthledPin = 15;

// Mode switch connection
int switchPin = 0;

LandjeRobot landjerobot(motor, LandjeRobotMotorController::STEPMODE::FULL_STEP, wheelRadiusMM , trackWidthMM, lineSensors, lineSensorInverse, ultraPin, servoPin, mouthledPin, switchPin);
```

These instructions must be placed in the program before the *setup()* function. Cut and paste these instructions into every program you write for the robot.

## The robot instructionset             

The Landje robot has several unique instructions. You have instructions to move, turn or,for example, to measure the distance. When you give these instructions the Landje Robot will then executed these instructions. You will see the line below in the first part of the program.

`LandjeRobot landjerobot(motor, LandjeRobotMotorController::STEPMODE::FULL_STEP, wheelRadiusMM ,
trackWidthMM, lineSensors, lineSensorInverse, ultraPin, servoPin,mouthledPin);`

With this long instruction the robot is set up. After executing this instruction you can use the variable `landjerobot` to give instructions to the robot. You give an instruction by adding the instruction to the variable `landjerobot`. You add an instruction to landjerobot by means of a dot. For example;  

`landjerobot.talk(5);` 

Pasting an instruction behind the variable `landjerobot`, is called *giving* an instruction. So if the instruction says '*give the instruction move*' you program `landjerobot.move()`. In the next section you will learn more about all the special instructions that the Landje robot understands. 

### The Landje robot instructionset

The Landje robot has several instructions. With some instructions you can or must give something extra to the instruction. For example, if you want the robot to move, you can tell it which direction to drive in. To tell something extra to an instruction is called *passing*. You *pass* to the instruction `move` which direction it should drive in.

`landjerobot.move(LandjeRobot::DIRECTION::FORWARD); `

With `LandjeRobot::DIRECTION::FORWARD` you pass to the land robot that it must move forward. You tell the LandjeRobot robot to move in the DIRECTION `FORWARD`. 

The information you pass on to the robot is called *parameter*. None, one or more parameters can be passed on to each instruction. How much and which parameters you can pass on differs per instruction.

Some instructions allow you to specify some parameters, but you don't have to. If you give the instruction `move` you may specify the parameter *waiting*, but it is not necessary. So you may give the instruction `landerobot.move(LandjeRobot::DIRECTION::FORWARD,10)` but also `landerobot.move(LandjeRobot::DIRECTION::FORWARD)`. At the first instruction the robot will drive 10 centimeters forward. On the second instruction the robot will continue to move forward until you give the instruction to stop. If you do not specify a parameter, a value will be selected. This value is called the *default* value. For the parameter *distance* this is infinite (∞). 

If you look up the parameter for instructions in this manual, there is one value for a parameter _underlined_. This is the *default* value that will be chosen for the parameter if you do not pass the parameter on to the instruction. Take a look at the instruction *move*, it shows the value '∞' which is underlined. The character '∞' means infinite. If you do not specify the parameter *distance*, the robot will continue to drive till you give another instruction to stop driving.

Instructions can also return a value. If an instruction returns a value, this is mentioned in the instruction documentation. The instruction *doIMove* has no parameters, but does return a value. If the robot moves you get *true*, otherwise *false*.
   
### Instructions

#### detectLine

**Description**

Indicates if a line on the floor is detected.

**Syntax**

detectLine();   

**Parameters**

none
        
**Returns**

|Type|Value|Comments|
|:---|:---|:---|
|| LandjeRobot::LINE::NONE</br>LandjeRobot::LINE::LEFT</br> LandjeRobot::LINE::RIGHT</br> LandjeRobot::LINE::BOTH | NONE indicates that no line is detected. BOTH is returned if the LEFT and RIGHT BOTH sensors do detect a line. |

**Example**

```

if (landjerobot.detectLine() != LandjeRobot::LINE::NONE) {
    Serial.println("Sensor detected a line");
}

```

#### doIMove

**Description**

Indicates if the robot is moving.

**Syntax**

doIMove();   

**Parameters**

none
        
**Returns**

|Type|Value|Comments|
|:---|:---|:---|
|bool| true | This value is returned if the robot is moving |
|bool| false | If the robot is not moving, this vallue is returned |

**Example**

```
// Move the robot in forward direction
landjerobot.move(LandjeRobot::DIRECTION::FORWARD);

if (landjerobot.doIMove()) {
    Serial.println("I am moving now!");
}

```

#### doITalk

**Description**

Indicates if the robot is talking.

**Syntax**

doITalk();   

**Parameters**

none
        
**Returns**

|Type|Value|Comments|
|:---|:---|:---|
|bool| true | This value is returned if the robot is talking. |
|bool| false | If the robot does not talk, this value is returned |

**Example**

```
// Make the robot talk for 60 seconds
landjerobot.talk(60);

if (landjerobot.doITalk()) {
    Serial.println("I am talking now!");
}

```

#### look

**Description**

Turn the robot head in a specific direction

**Syntax**

look( direction );   

**Parameters**

|Parameter|Type|Values|Comments|
|:---|:---|:---|:---|
| direction | | LandjeRobot::LOOK::FORWARD</br>LandjeRobot::LOOK::LEFT</br>LandjeRobot::LOOK::RIGHT</br>LandjeRobot::LOOK::FAR\_LEFT</br>LandjeRobot::LOOK::FAR\_RIGHT | |

**Look directions for the robot**
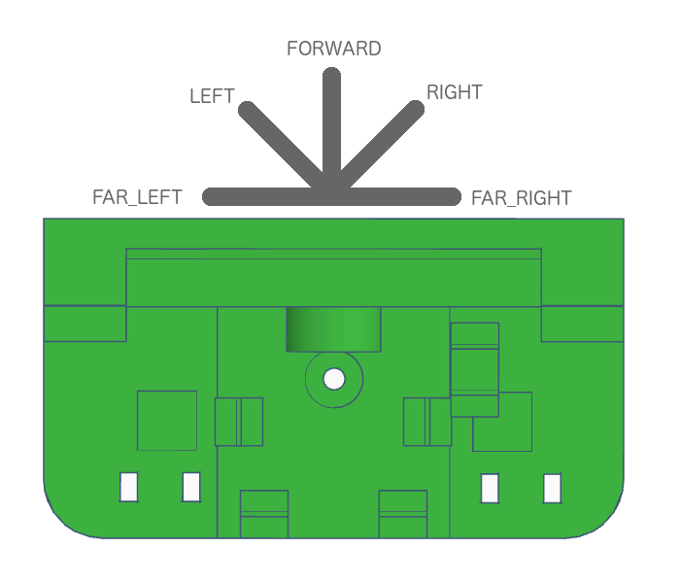
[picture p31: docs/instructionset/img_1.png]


**Returns**

nothing

**Example**

```
// Look left
landjerobot.look(LandjeRobot::LOOK::LEFT);
```

#### measureDistance

**Description**

Measures the distance between the robot and another object

**Syntax**

measureDistance();   

**Parameters**

none
        
**Returns**

|Type|Value|Comments|
|:---|:---|:---|
|int| 2..400 | Distance in centimetres |

**Example**

```
int measuredDistance = 0;
// Measure the distance between the robot and another object
measuredDistance  = landjerobot.measureDistance();

Serial.print("Measured distance ");
Serial.print(measuredDistance);
Serial.println(" cm");

```

#### mode

**Description**

Indicates the state of the mode switch.

**Syntax**

mode();   

**Parameters**

none
        
**Returns**

|Type|Value|Comments|
|:---|:---|:---|
|int| 1 | Switch has state 1 |
|int| 2 | Switch has state 2 |

**Example**

```
if (landjerobot.mode() == 1) {
    Serial.println("Mode 1");
} else {
    Serial.println("Mode 2");
}
```

#### mouthClosed

**Description**

Let the robot keep his mouth shut by turning off the led

**Syntax**

mouthClosed();   

**Parameters**

none
        
**Returns**

nothing

**Example**

```
// Shut the robots mouth
landjerobot.mouthClosed();
```

#### mouthOpen

**Description**

Let the robot open its mouth by turning on the led

**Syntax**

mouthOpen();   

**Parameters**

none
        
**Returns**

nothing

**Example**

```
// Let the robot open its mouth
landjerobot.mouthOpen();
```

#### move

**Description**

Move the robot in one direction

**Syntax**

move( direction );   
move( direction , distance);   
move( direction , distance, wait);

**Parameters**

|Parameter|Type|Values|Comments|
|:---|:---|:---|:---|
| direction | | LandjeRobot::DIRECTION::STOP </br>LandjeRobot::DIRECTION::FORWARD</br>LandjeRobot::DIRECTION::BACKWARD | |
| distance |int| 0 .. _∞_| The distance to be moved in centimetres |
| wait |bool| true</br>_false_ | Wait (true) by carrying out the next instruction until the specified distance has been covered |

**Returns**

nothing

**Example**

```
// robot moves in forward direction
landjerobot.move(LandjeRobot::DIRECTION::FORWARD);

// moves the robot 10cm backwards
landjerobot.move(LandjeRobot::DIRECTION::BACKWARD,10);

// move the robot 20cm in forward direction and 
// wait until the specified distance has been covered
landjerobot.move(LandjeRobot::DIRECTION::FORWARD,20,true);
```

#### talk

**Description**

Let the robot 'talk' by letting the led blink randomly

**Syntax**

talk( duration );   

**Parameters**

|Parameter|Type|Values|Comments|
|:---|:---|:---|:---|
| duration | int | 0..∞ | Duration the robot 'talks'|

**Returns**

nothing

**Example**

```
// Talk for 7 seconds
landjerobot.talk(7);
```

#### turn

**Description**

Turn the robot in a certain direction 

**Syntax**

turn( direction );   
turn( direction , angle);   
turn( direction , angle, wait);

**Parameters**

|Parameter|Type|Values|Comments|
|:---|:---|:---|:---|
| direction | | LandjeRobot::TURN::STRAIGHT</br>LandjeRobot::TURN::LEFT</br>LandjeRobot::TURN::RIGHT | The direction of rotation of the robot. The Value STRAIGHT resets the direction and makes the robot move straight forward or backward |
| hoek |int| 0..360 </br>_90_| The number of degrees the robot should rotate. An angle of 90 degrees is a right angle |
| wait |bool| true</br>_false_ | Wait (true) to carry out the following instruction until the specified distance has been covered |

**Turn directions of the robot**
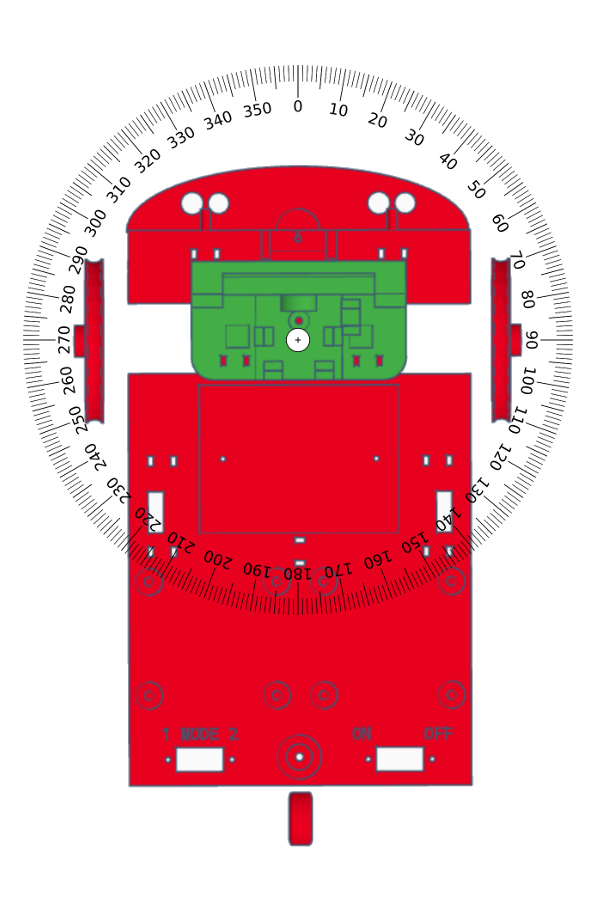
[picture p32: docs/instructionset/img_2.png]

        
**Returns**

nothing

**Example**

```
// turn the robot left in a right angle
landjerobot.turn(LandjeRobot::TURN::LEFT);

// rotate the robot 360 degrees around its axis 
landjerobot.turn(LandjeRobot::TURN::RIGHT,360);

```

## Arduino instructies

Arduino instructions are for all Arduino computers, so not especially for this robot. Where at Landje Robot instruction you have to type `landjerobot.` for the instruction, you don't have to and can't do this for Arduino instructions. With Arduino instructions you just use the instruction name.

If you want to learn more instructions from the Arduino, you can take a look at the [Arduino Language Referece](https://www.arduino.cc/reference/en/).

#### delay

**Description**

Wait a few milliseconds. Thousand (1000) milliseconds is equal to 1 second.

**Syntax**

delay( duration );   

**Parameters**

|Parameter|Type|Valuen|Comments|
|:---|:---|:---|:---|
| duration | int | 0..∞ | Number of milliseconds to wait.|

**Returns**

nothing

**Example**

```
// Wait 2 seconds
delay(2000); 
```

#### random

**Description**

Enter a random number

**Syntax**

random( smallest number, largest number );   

**Parameters**

|Parameter|Type|Valuen|Comments|
|:---|:---|:---|:---|
| smallest number | int | 0..∞ | Smallest number that can be returned as a random number |
| largest number | int | 0..∞ | Largest number that can be returned as a random number |

**Returns**

|Type|Value|Comments|
|:---|:---|:---|
|long| - | A random number equal to or greater than the smallest number specified and equal to or smaller than the largest number specified. |

The type ```long``` is niet explained. But for the robot, you can also use the type  ```int```.

**Example**

```
// Enter a random number,
// greater than or equal to 10 and
// Less than or equal to 20
int a = random(10,20); 
```

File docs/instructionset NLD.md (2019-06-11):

# Landje Robot Instructieset

De Landje robot heeft zijn eigen set van opdrachten die je hem kunt geven, een instructie-set.
Met deze instructies kun je de robot eenvoudig besturen.

Elke programma voor een Landje Robot moet beginnen met de volgende instructies. Deze instructies hoef je niet te begrijpen. Je kunt deze instructies gewoon boven aan elke robot programma plakken.

```
#include <LandjeRobot.h>

// Aansluitingen van de robot motors.
const int motor[2][4] = {
  {2, 3, 4, 5}, {6, 7, 8, 9}
} ;

// Aansluitingen van de lijn sensoren
const int lineSensors[2] = { 10, 11 } ;
// Lichte vloer met donker lijnen = true
// Donkere vloer met lichte lijnen = false 
const bool lineSensorInverse = true;

// Omtrek van de wielen in cm
const int wheelRadiusMM = 21 ;
// Afstand tussen de wielen in cm
const int trackWidthMM = 98 ;

// Aansluiting van de ultrasoon sensor
int ultraPin = 13 ;

// Aansluiting van de servo
int servoPin = 14 ;

// Aansluiting van het led 
int mouthledPin = 15 ;

// Aansluiting van de mode schakelaar
int switchPin = 0 ;

LandjeRobot landjerobot(motor, LandjeRobotMotorController::STEPMODE::FULL_STEP, wheelRadiusMM , trackWidthMM, lineSensors, lineSensorInverse, ultraPin, servoPin, mouthledPin, switchPin) ;
```

Deze instructies moeten voor de functie *setup()* in het programma geplaatst worden. Knip en plak deze instructies voor aan ieder programma dat je voor de robot schrijft.

## De robot instructie set             

De Landje robot heeft verschillende eigen instructies. Je hebt instructies om te bewegen, te draaien of bijvoorbeeld om de afstand te meten. Deze instructies geeft je aan de Landje Robot die deze instructies dan weer opvolgd. In het eerste gedeelte van het programma zie je als laatste regel staan. 

`LandjeRobot landjerobot(motor, LandjeRobotMotorController::STEPMODE::FULL_STEP, wheelRadiusMM ,
trackWidthMM, lineSensors, lineSensorInverse, ultraPin, servoPin,mouthledPin) ;`

Met deze lange instructie wordt de robot ingesteld. Na het uitvoeren van deze regel kun je de variabele `landjerobot` gebruiken om instructies aan de robot te geven. Je geeft een instructie door aan de variabele `landjerobot` de instructie te plakken. Je plakt een instructie aan landjerobot door middel van een punt. Bijvoorbeeld;   

`landjerobot.talk(5) ;` 

Het plakken van een instructie achter de variabele `landjerobot`, noem je het *geven* van een instructie. Als er dus ergens staat '*geef de instructie move*' programmeer je dus `landjerobot.move()`. In de volgende paragraaf leer je meer over alle speciale instructies die de Landje robot begrijpt. 

### De Landje robot instructieset

De Landje robot heeft verschillende instructies. Bij sommige instructies kun of moet je iets extra's aan de instructie doorgeven. Als je de robot wilt laten bewegen kun je bijvoorbeeld vertellen welke richting hij moet op rijden. Het iets extra's doorgeven aan een instructie noemen we *doorgeven*. Je *geeft* dus aan de instructie `move` *door* welke richting hij op moet rijden.

`landjerobot.move(LandjeRobot::DIRECTION::FORWARD) ; `

Met `LandjeRobot::DIRECTION::FORWARD` geef je aan de landjerobot door dat het vooruit moet bewegen. Het engelse woord `FORWARD` betekent vooruit, `DIRECTION` betekent richting. Je vertelt `LandjeRobot` robot dus dat hij in de `DIRECTION` `FORWARD` moet bewegen. 

Wat je aan de robot doorgeeft heet *parameter*. Aan elke instructie kan geen, één of meerdere parameters worden doorgegeven. Hoeveel en welke parameters je kan doorgeven verschilt per instructie.

Bij sommige instructies mag je sommige parameters opgegeven, maar hoeft dit niet. Als je de instructie `move` opgeeft mag je de parameter *wachten* opgeven, maar het hoeft niet. Je mag dus de instructie `landerobot.move(LandjeRobot::DIRECTION::FORWARD,10)` geven maar ook `landerobot.move(LandjeRobot::DIRECTION::FORWARD)`. Bij de eerste instructie zal de robot 10 centimeter vooruit gaan rijden. Bij de tweede instructie zal de robot net zolang vooruit blijven rijden totdat je de instructie geeft om te stoppen. Als je een parameter niet opgeeft zal een waarde gekozen worden. Deze gekozen waarde noemt men de *standaard* waarde. Voor de parameter *afstand* is dit oneindig (∞). 

Als je in deze handleiding de parameter voor instructies opzoekt is er één waarde voor een parameter _onderstreept_. Dit is de waarde welke voor de parameter gekozen zal worden als je de parameter niet doorgeeft aan de instructie. Kijk eens bij de instructie *move*, daar staat dat de waarde '∞' onderstreept. Het teken '∞' betekend oneindig. Als je de parameter *afstand* niet opgeeft blijft de robot oneindig doorrijden.

Instructies kunnen ook een waarde teruggeven. Als een instructie een waarde teruggeeft staat dit bij de instructie in de handleiding vermeld. De instructie *doIMove* heeft geen parameters, maar geeft wel een waarde terug. Als de robot beweegt krijg je *true*, anders *false*.
   
### Instructies

#### detectLine

**Omschrijving**

Geeft aan of er een lijn op de vloer wordt gedetecteerd

**Syntax**

detectLine() ;   

**Parameters**

geen
        
**Geeft terug**

|Type|Waarde|Opmerkingen|
|:---|:---|:---|
|| LandjeRobot::LINE::NONE</br>LandjeRobot::LINE::LEFT</br> LandjeRobot::LINE::RIGHT</br> LandjeRobot::LINE::BOTH | NONE geeft aan dat er geen lijn gedetecteerd wordt. Bij BOTH wordt zowel links als rechts een lijn gedetecteerd |

**Voorbeeld**

```

if (landjerobot.detectLine() != LandjeRobot::LINE::NONE) {
    Serial.println("Er is een lijn gedetecteerd") ;
}

```

#### doIMove

**Omschrijving**

Geeft aan of de robot beweegt.

**Syntax**

doIMove() ;   

**Parameters**

geen
        
**Geeft terug**

|Type|Waarde|Opmerkingen|
|:---|:---|:---|
|bool| true | Deze waarde wordt teruggegeven als de robot aan het bewegen is |
|bool| false | Als de robot niet beweegt wordt deze waarde teruggeveven |

**Voorbeeld**

```
// beweeg de robot vooruit
landjerobot.move(LandjeRobot::DIRECTION::FORWARD) ;

if (landjerobot.doIMove()) {
    Serial.println("Ik beweeg!") ;
}

```

#### doITalk

**Omschrijving**

Geeft aan of de robot aan het praten is.

**Syntax**

doITalk() ;   

**Parameters**

geen
        
**Geeft terug**

|Type|Waarde|Opmerkingen|
|:---|:---|:---|
|bool| true | Deze waarde wordt teruggegeven als de robot aan het praten is |
|bool| false | Als de robot niet praat wordt deze waarde teruggeveven |

**Voorbeeld**

```
// Laat de robot praten voor 60 seconden
landjerobot.talk(60) ;

if (landjerobot.doITalk()) {
    Serial.println("Ik praat!") ;
}

```

#### look

**Omschrijving**

Laat de robot in een richting kijken

**Syntax**

look( richting ) ;   

**Parameters**

|Parameter|Type|Waarden|Opmerkingen|
|:---|:---|:---|:---|
| richting | | LandjeRobot::LOOK::FORWARD</br>LandjeRobot::LOOK::LEFT</br>LandjeRobot::LOOK::RIGHT</br>LandjeRobot::LOOK::FAR\_LEFT</br>LandjeRobot::LOOK::FAR\_RIGHT | |

**Kijkrichtingen van de robot**


**Geeft terug**

niets

**Voorbeeld**

```
// Kijk naar links
landjerobot.look(LandjeRobot::LOOK::LEFT) ;
```

#### measureDistance

**Omschrijving**

Meet de afstand van de robot tot een ander object

**Syntax**

measureDistance() ;   

**Parameters**

geen
        
**Geeft terug**

|Type|Waarde|Opmerkingen|
|:---|:---|:---|
|int| 2..400 | Afstand in centimeters |

**Voorbeeld**

```
int gemetenAfstand = 0 ;
// Meet de afstand van de robot tot een ander object
gemetenAfstand  = landjerobot.measureDistance() ;

Serial.print("Gemeten afstand ") ;
Serial.print(gemetenAfstand) ;
Serial.println(" cm") ;

```

#### mode

**Omschrijving**

Geeft aan in welke stand de mode schakelaar staat.

**Syntax**

mode() ;   

**Parameters**

geen
        
**Geeft terug**

|Type|Waarde|Opmerkingen|
|:---|:---|:---|
|int| 1 | Schakelaar staat in stand 1 |
|int| 2 | Schakelaar staat in stand 2 |

**Voorbeeld**

```

if (landjerobot.mode() == 1) {
    Serial.println("Mode 1") ;
} else {
    Serial.println("Mode 2") ;
}

```

#### mouthClosed

**Omschrijving**

Laat de robot zijn mond 'dicht' doen door het led-je uit te zetten

**Syntax**

mouthClosed() ;   

**Parameters**

geen
        
**Geeft terug**

niets

**Voorbeeld**

```
// Laat de robot zijn mond dicht doen
landjerobot.mouthClosed();
```

#### mouthOpen

**Omschrijving**

Laat de robot zijn mond 'open' doen door het led-je aan te zetten

**Syntax**

mouthOpen() ;   

**Parameters**

geen
        
**Geeft terug**

niets

**Voorbeeld**

```
// Laat de robot zijn mond open doen
landjerobot.mouthOpen();
```

#### move

**Omschrijving**

Laat de robot in een richting bewegen

**Syntax**

move( richting ) ;   
move( richting , afstand) ;   
move( richting , afstand, wachten) ;

**Parameters**

|Parameter|Type|Waarden|Opmerkingen|
|:---|:---|:---|:---|
| richting | | LandjeRobot::DIRECTION::STOP </br>LandjeRobot::DIRECTION::FORWARD</br>LandjeRobot::DIRECTION::BACKWARD | |
| afstand |int| 0.. _∞_| De afstand die bewogen moet worden in centimeters |
| wachten |bool| true</br>_false_ | Wacht (true) met het uitvoeren van de volgende instructie totdat de opgegeven afstand is afgelegd |

**Geeft terug**

niets

**Voorbeeld**

```
// beweeg de robot vooruit
landjerobot.move(LandjeRobot::DIRECTION::FORWARD) ;

// beweeg de robot 10cm achteruit
landjerobot.move(LandjeRobot::DIRECTION::BACKWARD,10) ;

// beweeg de robot 20cm vooruit en wacht 
// totdat de opgegeven afstand is afgelegd
landjerobot.move(LandjeRobot::DIRECTION::FORWARD,20,true) ;

```

#### talk

**Omschrijving**

Laat de robot 'praten' door een lichtje in de mond te laten knipperen.

**Syntax**

talk( duur ) ;   

**Parameters**

|Parameter|Type|Waarden|Opmerkingen|
|:---|:---|:---|:---|
| duur | int | 0..∞ | Aantal seconden dat de robot 'praat'|

**Geeft terug**

niets

**Voorbeeld**

```
// Praat 7 seconden
landjerobot.talk(7);
```

#### turn

**Omschrijving**

Laat de robot in een bepaalde richting draaien 

**Syntax**

turn( richting ) ;   
turn( richting , hoek) ;   
turn( richting , hoek, wachten) ;

**Parameters**

|Parameter|Type|Waarden|Opmerkingen|
|:---|:---|:---|:---|
| richting | | LandjeRobot::TURN::STRAIGHT</br>LandjeRobot::TURN::LEFT</br>LandjeRobot::TURN::RIGHT | De draairichting van de robot. De waarde STRAIGHT laat de robot weer recht voor- of achteruit rijden |
| hoek |int| 0..360 </br>_90_| Het aantal graden dat de robot moet draaien. Een hoek van 90 graden is een rechte hoek |
| wachten |bool| true</br>_false_ | Wacht (true) met het uitvoeren van de volgende instructie totdat de opgegeven afstand is afgelegd |

**Draairichtingen van de robot**

        
**Geeft terug**

niets

**Voorbeeld**

```
// draai de robot naar links
landjerobot.turn(LandjeRobot::TURN::LEFT) ;

// laat de robot een rondje rechtsom draaien
landjerobot.turn(LandjeRobot::TURN::RIGHT,360) ;

```

## Arduino instructies

Arduino instructies zijn voor alle Arduino computers, dus niet speciaal voor deze robot. Waar je bij Landje Robot instructies `landjerobot.` voor de instructie moet typen, hoeft en kan dit niet voor Arduino instructies. Bij Arduino instructies gebruik je gewoon de instructienaam. 

Wil je meer instructies leren van de Arduino, dan kun je een kijkje nemen in de [Arduino Language Referece](https://www.arduino.cc/reference/en/).

#### delay

**Omschrijving**

Wacht een aantal milliseconden. Duizend (1000) milliseconden is gelijk aan 1 seconde.

**Syntax**

delay( duur ) ;   

**Parameters**

|Parameter|Type|Waarden|Opmerkingen|
|:---|:---|:---|:---|
| duur | int | 0..∞ | Aantal milliseconden dat er gewacht wordt.|

**Geeft terug**

niets

**Voorbeeld**

```
// Wacht twee seconden
delay(2000) ; 
```

#### random

**Omschrijving**

Geef een willekeurig getal

**Syntax**

random( kleinste getal, grootste getal ) ;   

**Parameters**

|Parameter|Type|Waarden|Opmerkingen|
|:---|:---|:---|:---|
| kleinste getal | int | 0..∞ | Kleinste waarde dat als willekeurg getal terugegeven kan worden |
| grootste getal | int | 0..∞ | Grootste waarde dat als willekeurg getal terugegeven kan worden |

**Geeft terug**

|Type|Waarde|Opmerkingen|
|:---|:---|:---|
|long| - | Een willekeurig getal gelijk of groter dan het opgegeven kleinste getal en gelijk of kleiner dan het opgegeven grootste getal. |

Het type ```long``` is niet uitgelegd. Maar voor de robot mag je ook het type ```int``` gebruiken.

**Voorbeeld**

```
// Geef een willeurig getal,
// groter of gelijk aan 10 en
// kleiner of gelijk aan 20
int a = random(10,20) ; 
```

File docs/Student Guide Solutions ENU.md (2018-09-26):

# Student Guide Solutions

## Lesson 3, variables

### Assignment 1

Create three variables and print the values

    /*
    
    */

    void setup() {
      Serial.begin(9600);
      delay(2000);
  
      String name = "Peter" ;
      int value = 12;
      boolean trueorfalse = false;

      Serial.println(name);
      Serial.println(value);
      Serial.println(trueorfalse);
    }

    void loop() {
    
    }

## Lesson 4, comparing

### Assignment 1

    /*

    */

    void setup() {
      Serial.begin(9600);
      delay(2000);

      String var1 = "abcd";    
      String var2 = "abcd";
      String var3 = "efgh";

      Serial.println(var1 == var2);
      Serial.println(var1 == var3);

    }

    void loop() {

    }

### Assignment 2  
    
    /*

    */

    void setup() {
      Serial.begin(9600);
      delay(2000);

      String var1 = "abcd";    
      String var2 = "abcd";
      String var3 = "efgh";
      boolean outcome = var1 == var2;

      Serial.println(var1 == var2);
      Serial.println(var1 == var3);
      Serial.println(outcome);
    }

    void loop() {

    }

### Assignment 3  
    
    /*

    */

    void setup() {
      Serial.begin(9600);
      delay(2000);

      int large = 2313;    
      int small = 5;    
      
      Serial.println(small > large);
      Serial.println(small < large);
    }

    void loop() {

    }

### Assignment 4
    
    /*

    */

    void setup() {
      Serial.begin(9600);
      delay(2000);

      int large = 2313;    
      int small = 5;    
      
      Serial.println(small > large);
      Serial.println(small < large);
      Serial.println(small >= small);
      Serial.println(large <= large);
      Serial.println(small >= large);
      Serial.println(large <= small);
    }

    void loop() {

    }

### Assignment 5
    
    /*

    */

    void setup() {
      Serial.begin(9600);
      delay(2000);

      int large = 2313;    
      int small = 5;    
      
      Serial.println(small > large);
      Serial.println(small < large);
      Serial.println(small >= small);
      Serial.println(large <= large);
      Serial.println(small >= large);
      Serial.println(large <= small);
      Serial.println(small != small);    
      Serial.println(small != large);          
    }

    void loop() {

    }

## Lesson 5, conditional statements

### Assignment 1

    /*

    */

    void setup() {
      Serial.begin(9600);
      delay(2000);

      int large = 2313;    
      int small = 5;    
      
      if (small < large) {
        Serial.println("small is smaller than large");      
      } 
    }

    void loop() {

    }
    
### Assignment 2

    /*

    */

    void setup() {
      Serial.begin(9600);
      delay(2000);

      int large = 2313;    
      int small = 5;    
      
      if (small < large) {
        Serial.println("small is smaller than large");      
      } else {
        Serial.println("small is larger than large");      
      }
    }

    void loop() {

    }    
    
## Lesson 6, Loops

### Assignment 1

The correct answer is 9x
    
    getal 1
    "I do repeat this" 
    getal 2
    "I do repeat this" 
    getal 3
    "I do repeat this" 
    getal 4
    "I do repeat this" 
    getal 5
    "I do repeat this" 
    getal 6
    "I do repeat this" 
    getal 7
    "I do repeat this" 
    getal 8
    "I do repeat this" 
    getal 9
    "I do repeat this" 
    getal 10

### Assignment 2

    /*

    */

    void setup() {
      Serial.begin(9600);
      delay(2000);
  
      int base = 3;
      int exponent = 5;
      int outcome = base;
  
      for (int x=1; x<exponent; x++) {
        outcome = outcome * base;
      }
  
      Serial.println(outcome);
    
    }

    void loop() {
    
    }

## Lesson 7, Debugging

### Assignment 1

### Assignment 2

    /*
    
    */
    
    void setup() {
      
      Serial.begin(9600);
      delay(2000);
      
      Serial.println("Is it going well?");
        
    }
    
    void loop() {
        
    }

### Assignment 3

#### Solution 1

    void setup() {
      Serial.begin(9600);
      delay(2000);
      pinMode(A1,INPUT);
      randomSeed(analogRead(A1)); 
  
      int getal = 10;
      Serial.println("start number");
      Serial.println(number);
  
      int counter = random(1, 10);
      Serial.println("start counter");
      Serial.println(counter);
      
      while (number != counter) {
        Serial.println("counter");
        Serial.println(counter);
        counter ++;
      }
  
      Serial.println("Finished !");
    
    }

    void loop() {
        
    }

#### Solution 2

    void setup() {
      Serial.begin(9600);
      delay(2000);
      pinMode(A1,INPUT);
      randomSeed(analogRead(A1)); 
  
      int number = 5;
      Serial.println("start number");
      Serial.println(number);
  
      int counter = random(1, 5);
      Serial.println("start counter");
      Serial.println(counter);
      
      while (number != counter) {
        Serial.println("counter");
        Serial.println(counter);
        counter ++;
      }
  
      Serial.println("Finished !");
    
    }

    void loop() {
        
    }
    
## Lesson 8, The Robot instructionset

### Assignment 1

    void setup() {
  
      landjerobot.move(LandjeRobot::DIRECTION::FORWARD,10);
    
    }

    void loop() {
    
    }
    
### Assignment 2

    void setup() {
    
      landjerobot.move(LandjeRobot::DIRECTION::FORWARD,10,true);
      landjerobot.turn(LandjeRobot::TURN::LEFT,90,true);
      landjerobot.move(LandjeRobot::DIRECTION::FORWARD,10,true);
      landjerobot.turn(LandjeRobot::TURN::LEFT,90,true);  
      landjerobot.move(LandjeRobot::DIRECTION::FORWARD,10,true);
      landjerobot.turn(LandjeRobot::TURN::LEFT,90,true);
      landjerobot.move(LandjeRobot::DIRECTION::FORWARD,10,true);
      landjerobot.turn(LandjeRobot::TURN::LEFT,90,true);

    }

    void loop() {
    
    }
    
### Assignment 3

    void setup() {
   
      ## Example 1
      for (int k=1; k <=4; k++) { 
        landjerobot.move(LandjeRobot::DIRECTION::FORWARD,10,true);
        landjerobot.turn(LandjeRobot::TURN::LEFT,90,true);
      }
   
      ## Example 2
      int k = 1;
      while (k <= 4) {
        landjerobot.move(LandjeRobot::DIRECTION::FORWARD,10,true);
        landjerobot.turn(LandjeRobot::TURN::LEFT,90,true);
        k++;
     }
   
    }

    void loop() {
    
    }
    
### Assignment 4

Hands on assignment, no specific solution

### Assignment 5

    void setup() {
   
      landjerobot.move(LandjeRobot::DIRECTION::FORWARD);
  
    }

    void loop() {
  
      if (landjerobot.detectLine() != LandjeRobot::LINE::NONE ) {
        landjerobot.move(LandjeRobot::DIRECTION::STOP );
      }
  
    }
    
## Lesson 9, Line Following   
    
### Assignment 1

    void setup() {
   
       landjerobot.move(LandjeRobot::DIRECTION::FORWARD);
  
    }

    void loop() {
  
      if (landjerobot.detectLine() != LandjeRobot::LINE::NONE) {
    
        if (landjerobot.detectLine() == LandjeRobot::LINE::LEFT) {
          landjerobot.turn(LandjeRobot::TURN::LEFT,10,true);      
        }
    
        if (landjerobot.detectLine() == LandjeRobot::LINE::RIGHT) {
          landjerobot.turn(LandjeRobot::TURN::RIGHT,10,true);
        }
    
        landjerobot.move(LandjeRobot::DIRECTION::FORWARD);
    
      }
  
    }

### Assignment 2

When the robot detects the a line with the left or right sensor. Then wait a short moment to see if the status of the line-detection sensor changes. When the robot arrives at the turn marker in a slightly slanting line the state of the sensor will change from `LandjeRobot::LINE::LEFT` or `LandjeRobot::LINE::RIGHT` to `
LandjeRobot::LINE::BOTH`. So when before taking action on the sensors output is waited for a fraction of a second, the turn marker will be detected correctly.

How this will be implemented is part of the next assignment. 

### Assignment 3

    void setup() {

       // Start moving when the robot is switched on,
       // do not wait
       landjerobot.move(LandjeRobot::DIRECTION::FORWARD);
  
    }

    void loop() {

      // If there is not nothing (!) detected by the
      // reflection sensors, then do something
      if (landjerobot.detectLine() != LandjeRobot::LINE::NONE) {
    
        // wait 30 milliseconds (0,03 second)
        delay(30);
    
        // When both reflection sensors do detect a line
        if (landjerobot.detectLine() == LandjeRobot::LINE::BOTH) {
          // turn the robot around and wait for completion
          landjerobot.turn(LandjeRobot::TURN::LEFT,180,true);
        }
    
        // When the reflection sensors do detect a line on the left
        if (landjerobot.detectLine() == LandjeRobot::LINE::LEFT) {
          // Turn 10 degrees to the left and wait for completion
          landjerobot.turn(LandjeRobot::TURN::LEFT,10,true);
        }
    
        // When the reflection sensors do detect a line on the right
        if (landjerobot.detectLine() == LandjeRobot::LINE::RIGHT) {
          // Turn 10 degrees to the right and wait for completion
          landjerobot.turn(LandjeRobot::TURN::RIGHT,10,true);
        }
    
        // Let the robot continue moving forward
        landjerobot.move(LandjeRobot::DIRECTION::FORWARD);
    
      } // end if
  
    }

### Assignment 4

```
int mode = 0;

void setup() {

  // read the mode-switch state
  mode = landjerobot.mode();

  // If the switch has state "1" 
  if (mode == 1) {
    // Start moving forward when the robot is switched on
    // and do not wait for completion of the instruction
    landjerobot.move(LandjeRobot::DIRECTION::FORWARD);
  }
  
}

void loop() {

  // If the switch has state "1" 
  if (mode == 1) {
    // If there is not nothing (!) detected by the
    // reflection sensors, then do something
    if (landjerobot.detectLine() != LandjeRobot::LINE::NONE) {
      
      // wait 30 milliseconds (0,03 second)
      delay(30);
      
      // When both reflection sensors do detect a line
      if (landjerobot.detectLine() == LandjeRobot::LINE::BOTH) {
        // turn the robot around and wait for completion
          landjerobot.turn(LandjeRobot::TURN::LEFT,180,true);
      }
      
      // When the reflection sensors do detect a line on the left
      if (landjerobot.detectLine() == LandjeRobot::LINE::LEFT) {
        // Turn 10 degrees to the left and wait for completion
        landjerobot.turn(LandjeRobot::TURN::LEFT,10,true);
      }
      
      // When the reflection sensors do detect a line on the right
      if (landjerobot.detectLine() == LandjeRobot::LINE::RIGHT) {
        // Turn 10 degrees to the right and wait for completion
        landjerobot.turn(LandjeRobot::TURN::RIGHT,10,true);
      }
      
      // Let the robot continue moving forward
      landjerobot.move(LandjeRobot::DIRECTION::FORWARD);
      
    } // end if
  } else { // If the switch has state "2" 

  }
  
}
```

## Lesson 10, more sensors and motors

### Assignment 1

```
void setup() {

    landjerobot.look(LandjeRobot::LOOK::FORWARD);
}

void loop() {
    
}
```

```
void setup() {

    landjerobot.look(LandjeRobot::LOOK::FAR_LEFT);
    delay(2000);
    landjerobot.look(LandjeRobot::LOOK::FORWARD);
    delay(2000);
    landjerobot.look(LandjeRobot::LOOK::FAR_RIGHT);

}

void loop() {
    
}
```

### Assignment 2

```
void setup() {
  
   landjerobot.mouthOpen();
   delay(5000);
   landjerobot.mouthClosed();
   delay(5000);
   
   landjerobot.talk(10);
    
}
```

### Assignment 3

Sound travels at the speed of 343 m/sec. So when it takes 12 seconds to hear the echo, the sound has travelled 343 * 12 or 4116 meters. But the sound has to travel from you to the mountain and back again. Therefore the actual distance to the mountain is 4116 meters divided by 2. So the distance is 2058 meters or approximately 2 km.

### Assignment 4

```
void setup() {

    int distance = 400;
  
    Serial.begin(9600);
    delay(2000);
    
    // Print de measured distance as long as
    // the distance is larger than 5cm.
    while (distance > 5) {
      distance = landjerobot.measureDistance();
      Serial.println(distance);
    }
    
    // Make the robot talk for 10 seconds
    landjerobot.talk(10);
    
}
```

## Lesson 11, A new program

### Assignment 1

Solution is;

* If the left sensor detects a line move 10cm backward, then turn 45 degrees right. Continue driving forward.
* If the right sensor detects a line move 10cm backward, then turn 45 degrees left. Continue driving forward.
* If the both sensors detect a line move 10cm backward, then turn 180 degrees left. Continue driving forward.

### Assignment 2

The robot must start moving forward when the mode switch is set to mode "2" and switched on. So in the function ```setup()``` and instruction has to be added to make the robot moving forward.

This can be accomplished in two ways. First by adding an if statement which will make the robot move forward in mode 2.

```
void setup() {

  // read the mode-switch state
  mode = landjerobot.mode();

  // If the switch has state "1" 
  if (mode == 1) {
    // Start moving forward when the robot is switched on
    // and do not wait for completion of the instruction
    landjerobot.move(LandjeRobot::DIRECTION::FORWARD);
  } else {
    // If the switch has state "2" 
    // Start moving forward when the robot is switched on
    // and do not wait for completion of the instruction
    landjerobot.move(LandjeRobot::DIRECTION::FORWARD);
  }
  
}
```

The same result can be accomplished by removing some lines of code from the existing code. Regardless of the state of the mode switch the robot has to start moving forward. There is no specific reason 

```
void setup() {

  // read the mode-switch state
  mode = landjerobot.mode();

  // Start moving forward when the robot is switched on
  // and do not wait for completion of the instruction
  landjerobot.move(LandjeRobot::DIRECTION::FORWARD);
  
}
```

### Assignment 3

This is a basic working example to make the robot stay within the lines. 

```
    // If there is not nothing (!) detected by the
    // reflection sensors, then do something
    if (landjerobot.detectLine() != LandjeRobot::LINE::NONE) {
      
      // wait 30 milliseconds (0,03 second)
      delay(30);
      
      // When both reflection sensors do detect a line
      if (landjerobot.detectLine() == LandjeRobot::LINE::BOTH) {
        // turn the robot around and wait for completion
          landjerobot.turn(LandjeRobot::TURN::LEFT,180,true);
      }
      
      // When the reflection sensors do detect a line on the left
      if (landjerobot.detectLine() == LandjeRobot::LINE::LEFT) {
        // Turn 10 degrees to the left and wait for completion
        landjerobot.turn(LandjeRobot::TURN::LEFT,10,true);
      }
      
      // When the reflection sensors do detect a line on the right
      if (landjerobot.detectLine() == LandjeRobot::LINE::RIGHT) {
        // Turn 10 degrees to the right and wait for completion
        landjerobot.turn(LandjeRobot::TURN::RIGHT,10,true);
      }
      
      // Let the robot continue moving forward
      landjerobot.move(LandjeRobot::DIRECTION::FORWARD);
      
    } // end if
```

Using the basic code, the robot may end in an endless loop, repeating the same movements over and over again. Most certainly this will occur when the robot ends up in a corner of the drawn rectangle. Adding some randomness whill resolve this issue.

```
    // If there is not nothing (!) detected by the
    // reflection sensors, then do something
    if (landjerobot.detectLine() != LandjeRobot::LINE::NONE) {
    
      // wait 30 milliseconds (0,03 second)
      delay(30);
    
      if (landjerobot.detectLine() == LandjeRobot::LINE::LEFT) {
        landjerobot.move(LandjeRobot::DIRECTION::BACKWARD, random(5,10), true);
        landjerobot.turn(LandjeRobot::TURN::RIGHT, random(20,90), true);
      }

      if (landjerobot.detectLine() == LandjeRobot::LINE::RIGHT) {
        landjerobot.move(LandjeRobot::DIRECTION::BACKWARD, random(5,10), true);
        landjerobot.turn(LandjeRobot::TURN::LEFT, random(20,90), true);
      }

      if (landjerobot.detectLine() == LandjeRobot::LINE::BOTH) {
        landjerobot.move(LandjeRobot::DIRECTION::BACKWARD, random(5,10), true);
        landjerobot.turn(LandjeRobot::TURN::LEFT, random(160,200), true);
      }
      
      landjerobot.move(LandjeRobot::DIRECTION::FORWARD);
    } // end if
```

### Assignment 4

```
void setup() {

  // read the mode-switch state
  mode = landjerobot.mode();

  // Make the robot look forward
  landjerobot.look(LandjeRobot::LOOK::FORWARD);
  
  // Start moving forward when the robot is switched on
  // and do not wait for completion of the instruction
  landjerobot.move(LandjeRobot::DIRECTION::FORWARD);
  
}
```

### Assignment 5

```
    // Measure the distance
    int distance = landjerobot.measureDistance();

    // Stop when the distance is less than 10cm
    if (distance < 10) {
      landjerobot.move(LandjeRobot::DIRECTION::STOP);
    }
```

### Assignment 6

To which direction would you send the robot; To the left

Based on distance; The longest measured distance.

```
    // Measure the distance
    int distance = landjerobot.measureDistance();

    // Stop when the distance is less than 10cm
    if (distance < 10) {
      landjerobot.move(LandjeRobot::DIRECTION::STOP);
      
      // Measure the distance to the left
      landjerobot.look(LandjeRobot::LOOK::LEFT);
      delay(1000);
      int left = landjerobot.measureDistance();

      // Measure the distance to the right
      landjerobot.look(LandjeRobot::LOOK::RIGHT);
      delay(1000);
      int right = landjerobot.measureDistance();
      
      // Look forward again
      landjerobot.look(LandjeRobot::LOOK::FORWARD);
      
      if (left > right) {
        landjerobot.turn(LandjeRobot::TURN::LEFT, 45, true);
      } else {
        landjerobot.turn(LandjeRobot::TURN::RIGHT, 45, true);
      }
      
      // move forward again
      landjerobot.move(LandjeRobot::DIRECTION::FORWARD);
    } // end if
  }
```

#Lesson 12, improvements

##Assignment 1

When the robot needs to turn, just move a bit backward first to get some space to turn.

```
    // Measure the distance
    int distance = landjerobot.measureDistance();

    // Stop when the distance is less than 10cm
    if (distance < 10) {
    
      // Stop moving
      landjerobot.move(LandjeRobot::DIRECTION::STOP);
      
      // Measure the distance to the left
      landjerobot.look(LandjeRobot::LOOK::LEFT);
      delay(1000);
      int left = landjerobot.measureDistance();

      // Measure the distance to the right
      landjerobot.look(LandjeRobot::LOOK::RIGHT);
      delay(1000);
      int right = landjerobot.measureDistance();
      
      // Look forward again
      landjerobot.look(LandjeRobot::LOOK::FORWARD);
      
      // Move a bit backward and turn to the left or right
      if (left > right) {
        landjerobot.move(LandjeRobot::DIRECTION::BACKWARD, 10, true);
        landjerobot.turn(LandjeRobot::TURN::LEFT, 45, true);
      } else {
        landjerobot.move(LandjeRobot::DIRECTION::BACKWARD, 10, true);
        landjerobot.turn(LandjeRobot::TURN::RIGHT, 45, true);
      }
      
      // Move forward again
      landjerobot.move(LandjeRobot::DIRECTION::FORWARD);
    } // end if
  }
```

Or more efficient

```
    // Measure the distance
    int distance = landjerobot.measureDistance();

    // Stop when the distance is less than 10cm
    if (distance < 10) {
      // Stop moving
      landjerobot.move(LandjeRobot::DIRECTION::STOP);
      
      // Measure the distance to the left
      landjerobot.look(LandjeRobot::LOOK::LEFT);
      delay(1000);
      int left = landjerobot.measureDistance();

      // Measure the distance to the right
      landjerobot.look(LandjeRobot::LOOK::RIGHT);
      delay(1000);
      int right = landjerobot.measureDistance();
      
      // Look forward again
      landjerobot.look(LandjeRobot::LOOK::FORWARD);
      
      // Move a bit backward
      landjerobot.move(LandjeRobot::DIRECTION::BACKWARD, 10, true);
      
      // Turn to the left or right
      if (left > right) {
        landjerobot.turn(LandjeRobot::TURN::LEFT, 45, true);
      } else {
        landjerobot.turn(LandjeRobot::TURN::RIGHT, 45, true);
      }
      
      // Move forward again
      landjerobot.move(LandjeRobot::DIRECTION::FORWARD);
    } // end if
  }
```

## Assignment 2

```
    // Measure the distance
    int distance = landjerobot.measureDistance();

    // Stop when the distance is less than 10cm
    if (distance < 10) {
    
      // Stop moving
      landjerobot.move(LandjeRobot::DIRECTION::STOP);
   
      // Grumble
      landjerobot.talk(5);
              
      // Measure the distance to the left
      landjerobot.look(LandjeRobot::LOOK::LEFT);
      delay(1000);
      int left = landjerobot.measureDistance();

      // Measure the distance to the right
      landjerobot.look(LandjeRobot::LOOK::RIGHT);
      delay(1000);
      int right = landjerobot.measureDistance();
      
      // Look forward again
      landjerobot.look(LandjeRobot::LOOK::FORWARD);
      
      // Move a bit backward
      landjerobot.move(LandjeRobot::DIRECTION::BACKWARD, 10, true);
      
      // Turn to the left or right
      if (left > right) {
        landjerobot.turn(LandjeRobot::TURN::LEFT, 45, true);
      } else {
        landjerobot.turn(LandjeRobot::TURN::RIGHT, 45, true);
      }
      
      // Move forward again
      landjerobot.move(LandjeRobot::DIRECTION::FORWARD);
    } // end if
  }
```

## Assignment 3

```
    // Measure the distance
    int distance = landjerobot.measureDistance();

    // Stop when the distance is less than 10cm
    if (distance < 10) {
      
      // Verifiy the measured distance
      int totaldistance = 0;
      for (int x=1; x<=5;x++) {
        totaldistance = totaldistance + landjerobot.measureDistance(); 
      }
      
      if (totaldistance < 50) {
      
        // Stop moving
        landjerobot.move(LandjeRobot::DIRECTION::STOP);
        
        // Grumble
        landjerobot.talk(5);
      
        // Measure the distance to the left
        landjerobot.look(LandjeRobot::LOOK::LEFT);
        delay(1000);
        int left = landjerobot.measureDistance();
  
        // Measure the distance to the right
        landjerobot.look(LandjeRobot::LOOK::RIGHT);
        delay(1000);
        int right = landjerobot.measureDistance();
        
        // Look forward again
        landjerobot.look(LandjeRobot::LOOK::FORWARD);
        
        // Move a bit backward
        landjerobot.move(LandjeRobot::DIRECTION::BACKWARD, 10, true);
      
        // Turn to the left or right
        if (left > right) {
          landjerobot.turn(LandjeRobot::TURN::LEFT, 45, true);
        } else {
          landjerobot.turn(LandjeRobot::TURN::RIGHT, 45, true);
        }
        
         // Move forward again
         landjerobot.move(LandjeRobot::DIRECTION::FORWARD);
      } // end if
    }
```

#Appendix

## Solution example

```

#include <LandjeRobot.h>

// Robot motor connections
const int motor[2][4] = {
  {2, 3, 4, 5}, {6, 7, 8, 9}
};

// Line sensor connections
const int lineSensors[2] = { 10, 11 };
// Light floor with dark lines = true
// Dark floor with light lines = false 
const bool lineSensorInverse = true;

// Wheel circumference in cm
const int wheelRadiusMM = 21;
// Track width in cm
const int trackWidthMM = 98;

// Ultrasonic sensor connections
int ultraPin = 13;

// Servo connections
int servoPin = 14;

// Led connection
int mouthledPin = 15;

// Mode switch connection
int switchPin = 0;

LandjeRobot landjerobot(motor, LandjeRobotMotorController::STEPMODE::FULL_STEP, wheelRadiusMM , trackWidthMM, lineSensors, lineSensorInverse, ultraPin, servoPin, mouthledPin, switchPin);

int mode = 0;

void setup() {

  // read the mode-switch state
  mode = landjerobot.mode();

  // Laat de robot naar voren kijken
  landjerobot.look(LandjeRobot::LOOK::FORWARD);
  
  // Start moving forward when the robot is switched on
  // and do not wait for completion of the instruction
  landjerobot.move(LandjeRobot::DIRECTION::FORWARD);
  
}

void loop() {

  // If the switch has state "1" 
  if (mode == 1) {
    // If there is not nothing (!) detected by the
    // reflection sensors, then do something
    if (landjerobot.detectLine() != LandjeRobot::LINE::NONE) {
      
      // wait 30 milliseconds (0,03 second)
      delay(30);
      
      // When both reflection sensors do detect a line
      if (landjerobot.detectLine() == LandjeRobot::LINE::BOTH) {
        // turn the robot around and wait for completion
          landjerobot.turn(LandjeRobot::TURN::LEFT,180,true);
      }
      
      // When the reflection sensors do detect a line on the left
      if (landjerobot.detectLine() == LandjeRobot::LINE::LEFT) {
        // Turn 10 degrees to the left and wait for completion
        landjerobot.turn(LandjeRobot::TURN::LEFT,10,true);
      }
      
      // When the reflection sensors do detect a line on the right
      if (landjerobot.detectLine() == LandjeRobot::LINE::RIGHT) {
        // Turn 10 degrees to the right and wait for completion
        landjerobot.turn(LandjeRobot::TURN::RIGHT,10,true);
      }
      
      // Let the robot continue moving forward
      landjerobot.move(LandjeRobot::DIRECTION::FORWARD);
      
    } // end if
    
  } else { // Als de schakelaar op "2" staat
  
    // If there is not nothing (!) detected by the
    // reflection sensors, then do something
    if (landjerobot.detectLine() != LandjeRobot::LINE::NONE) {
    
      // wait 30 milliseconds (0,03 second)
      delay(30);
    
      if (landjerobot.detectLine() == LandjeRobot::LINE::LEFT) {
        landjerobot.move(LandjeRobot::DIRECTION::BACKWARD, random(5,10), true);
        landjerobot.turn(LandjeRobot::TURN::RIGHT, random(20,90), true);
      }

      if (landjerobot.detectLine() == LandjeRobot::LINE::RIGHT) {
        landjerobot.move(LandjeRobot::DIRECTION::BACKWARD, random(5,10), true);
        landjerobot.turn(LandjeRobot::TURN::LEFT, random(20,90), true);
      }

      if (landjerobot.detectLine() == LandjeRobot::LINE::BOTH) {
        landjerobot.move(LandjeRobot::DIRECTION::BACKWARD, random(5,10), true);
        landjerobot.turn(LandjeRobot::TURN::LEFT, random(160,200), true);
      }
      
      landjerobot.move(LandjeRobot::DIRECTION::FORWARD);
    } // end if
  
    // Measure the distance
    int distance = landjerobot.measureDistance();

    // Stop when the distance is less than 10cm
    if (distance < 10) {
      
      // Verifiy the measured distance
      int totaldistance = 0;
      for (int x=1; x<=5;x++) {
        totaldistance = totaldistance + landjerobot.measureDistance(); 
      }
      
      if (totaldistance < 50) {
      
        // Stop moving
        landjerobot.move(LandjeRobot::DIRECTION::STOP);
        
        // Grumble
        landjerobot.talk(5);
      
        // Measure the distance to the left
        landjerobot.look(LandjeRobot::LOOK::LEFT);
        delay(1000);
        int left = landjerobot.measureDistance();
  
        // Measure the distance to the right
        landjerobot.look(LandjeRobot::LOOK::RIGHT);
        delay(1000);
        int right = landjerobot.measureDistance();
        
        // Look forward again
        landjerobot.look(LandjeRobot::LOOK::FORWARD);
        
        // Move a bit backward
        landjerobot.move(LandjeRobot::DIRECTION::BACKWARD, 10, true);
      
        // Turn to the left or right
        if (left > right) {
          landjerobot.turn(LandjeRobot::TURN::LEFT, 45, true);
        } else {
          landjerobot.turn(LandjeRobot::TURN::RIGHT, 45, true);
        }
        
         // Move forward again
         landjerobot.move(LandjeRobot::DIRECTION::FORWARD);
      }
    }
  }
}
```

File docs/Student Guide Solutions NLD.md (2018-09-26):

# Studenten Handboek Oplossingen

## Les 3, variabelen

### Opdracht 1

Maak drie variabelen en druk deze af

    /*
    
    */

    void setup() {
      Serial.begin(9600);
      delay(2000);
  
      String naam = "Peter" ;
      int waarde = 12;
      boolean waarofniet = false;

      Serial.println(naam);
      Serial.println(waarde);
      Serial.println(waarofniet);
    }

    void loop() {
    
    }

## Les 4, vergelijken

### Opdracht 1

    /*

    */

    void setup() {
      Serial.begin(9600);
      delay(2000);

      String var1 = "abcd";    
      String var2 = "abcd";
      String var3 = "efgh";

      Serial.println(var1 == var2);
      Serial.println(var1 == var3);

    }

    void loop() {

    }

### Opdracht 2  
    
    /*

    */

    void setup() {
      Serial.begin(9600);
      delay(2000);

      String var1 = "abcd";    
      String var2 = "abcd";
      String var3 = "efgh";
      boolean uitkomst = var1 == var2;

      Serial.println(var1 == var2);
      Serial.println(var1 == var3);
      Serial.println(uitkomst);
    }

    void loop() {

    }

### Opdracht 3  
    
    /*

    */

    void setup() {
      Serial.begin(9600);
      delay(2000);

      int groot = 2313;    
      int klein = 5;    
      
      Serial.println(klein > groot);
      Serial.println(klein < groot);
    }

    void loop() {

    }

### Opdracht 4
    
    /*

    */

    void setup() {
      Serial.begin(9600);
      delay(2000);

      int groot = 2313;    
      int klein = 5;    
      
      Serial.println(klein > groot);
      Serial.println(klein < groot);
      Serial.println(klein >= klein);
      Serial.println(groot <= groot);
      Serial.println(klein >= groot);
      Serial.println(groot <= klein);
    }

    void loop() {

    }

### Opdracht 5
    
    /*

    */

    void setup() {
      Serial.begin(9600);
      delay(2000);

      int groot = 2313;    
      int klein = 5;    
      
      Serial.println(klein > groot);
      Serial.println(klein < groot);
      Serial.println(klein >= klein);
      Serial.println(groot <= groot);
      Serial.println(klein >= groot);
      Serial.println(groot <= klein);
      Serial.println(klein != klein);    
      Serial.println(klein != groot);          
    }

    void loop() {

    }

## Les 5, voorwaardelijke statements

### Opdracht 1

    /*

    */

    void setup() {
      Serial.begin(9600);
      delay(2000);

      int groot = 2313;    
      int klein = 5;    
      
      if (klein < groot) {
        Serial.println("klein is kleiner dan groot");      
      } 
    }

    void loop() {

    }
    
### Opdracht 2

    /*

    */

    void setup() {
      Serial.begin(9600);
      delay(2000);

      int groot = 2313;    
      int klein = 5;    
      
      if (klein < groot) {
        Serial.println("klein is kleiner dan groot");      
      } else {
        Serial.println("klein is groter dan groot");      
      }
    }

    void loop() {

    }    
    
## Les 6, Herhalingen 

### Opdracht 1

Het juiste antwoord is 9x
    
    getal 1
    "Dit herhaal ik" 
    getal 2
    "Dit herhaal ik" 
    getal 3
    "Dit herhaal ik" 
    getal 4
    "Dit herhaal ik" 
    getal 5
    "Dit herhaal ik" 
    getal 6
    "Dit herhaal ik" 
    getal 7
    "Dit herhaal ik" 
    getal 8
    "Dit herhaal ik" 
    getal 9
    "Dit herhaal ik" 
    getal 10

### Opdracht 2

    /*

    */

    void setup() {
      Serial.begin(9600);
      delay(2000);
  
      int grondtal = 3;
      int exponent = 5;
      int uitkomst = grondtal;
  
      for (int x=1; x<exponent; x++) {
        uitkomst = uitkomst * grondtal;
      }
  
      Serial.println(uitkomst);
    
    }

    void loop() {
    
    }

## Les 7, Debuggen

### Opdracht 1

### Opdracht 2

    /*
    
    */
    
    void setup() {
      
      Serial.begin(9600);
      delay(2000);
      
      Serial.println("Gaat het wel goed?");
        
    }
    
    void loop() {
        
    }

### Opdracht 3

#### Oplossing 1

    void setup() {
      Serial.begin(9600);
      delay(2000);
      pinMode(A1,INPUT);
      randomSeed(analogRead(A1)); 
  
      int getal = 10;
      Serial.println("start getal");
      Serial.println(getal);
  
      int teller = random(1, 10);
      Serial.println("start teller");
      Serial.println(teller);
      
      while (getal != teller) {
        Serial.println("teller");
        Serial.println(teller);
        teller++;
      }
  
      Serial.println("Klaar!");
    
    }

    void loop() {
        
    }

#### Oplossing 2

    void setup() {
      Serial.begin(9600);
      delay(2000);
      pinMode(A1,INPUT);
      randomSeed(analogRead(A1)); 
  
      int getal = 5;
      Serial.println("start getal");
      Serial.println(getal);
  
      int teller = random(1, 5);
      Serial.println("start teller");
      Serial.println(teller);
      
      while (getal != teller) {
        Serial.println("teller");
        Serial.println(teller);
        teller++;
      }
  
      Serial.println("Klaar!");
    
    }

    void loop() {
        
    }
    
## Les 8, The Robot instructionset

### Opdracht 1

    void setup() {
  
      landjerobot.move(LandjeRobot::DIRECTION::FORWARD,10);
    
    }

    void loop() {
    
    }
    
### Opdracht 2

    void setup() {
    
      landjerobot.move(LandjeRobot::DIRECTION::FORWARD,10,true);
      landjerobot.turn(LandjeRobot::TURN::LEFT,90,true);
      landjerobot.move(LandjeRobot::DIRECTION::FORWARD,10,true);
      landjerobot.turn(LandjeRobot::TURN::LEFT,90,true);  
      landjerobot.move(LandjeRobot::DIRECTION::FORWARD,10,true);
      landjerobot.turn(LandjeRobot::TURN::LEFT,90,true);
      landjerobot.move(LandjeRobot::DIRECTION::FORWARD,10,true);
      landjerobot.turn(LandjeRobot::TURN::LEFT,90,true);
  
    }

    void loop() {
    
    }
    
### Opdracht 3

    void setup() {
   
      ## Voorbeeld 1
      for (int k=1; k <=4; k++) { 
        landjerobot.move(LandjeRobot::DIRECTION::FORWARD,10,true);
        landjerobot.turn(LandjeRobot::TURN::LEFT,90,true);
      }
   
      ## Voorbeeld 2
      int k = 1;
      while (k <= 4) {
        landjerobot.move(LandjeRobot::DIRECTION::FORWARD,10,true);
        landjerobot.turn(LandjeRobot::TURN::LEFT,90,true);
        k++;
     }
   
    }

    void loop() {
    
    }
    
### Opdracht 4

Geen specifieke oplossing

### Opdracht 5

    void setup() {
   
      landjerobot.move(LandjeRobot::DIRECTION::FORWARD);
  
    }

    void loop() {
  
      if (landjerobot.detectLine() != LandjeRobot::LINE::NONE ) {
        landjerobot.move(LandjeRobot::DIRECTION::STOP );
      }
  
    }
    
## Les 9, Lijnen volgen 
    
### Opdracht 1

    void setup() {
   
       landjerobot.move(LandjeRobot::DIRECTION::FORWARD);
  
    }

    void loop() {
  
      if (landjerobot.detectLine() != LandjeRobot::LINE::NONE) {
    
        if (landjerobot.detectLine() == LandjeRobot::LINE::LEFT) {
          landjerobot.turn(LandjeRobot::TURN::LEFT,10,true);      
        }
    
        if (landjerobot.detectLine() == LandjeRobot::LINE::RIGHT) {
          landjerobot.turn(LandjeRobot::TURN::RIGHT,10,true);
        }
    
        landjerobot.move(LandjeRobot::DIRECTION::FORWARD);
    
      }
  
    }

### Opdracht 2

Als de robot met de linker of rechter sensor een lijn detecteert (ziet). Wacht dan even om te kijken of de status van de sensor wijzigt. Wanneer de robot bij de draai markerking een beetje schuint aankomt zal de status van de sensor dan wijzigen van `LandjeRobot::LINE::LEFT` of `LandjeRobot::LINE::RIGHT` naar `
LandjeRobot::LINE::BOTH`. Dus als je heel even wacht voordat je reageert op de status van een sensor, zal de draai markering juist gedetecteerd worden.

Hoe je dit moet gaan programmeren is onderdeel van de volgende opdracht.

### Opdracht 3

    void setup() {

       // Start met rijden als de robot aangezet wordt en
       // wacht niet
       landjerobot.move(LandjeRobot::DIRECTION::FORWARD);
  
    }

    void loop() {

      // Als er niet niets (!) gedetecteerd wordt door de 
      // reflectie sensors doe dan iets
      if (landjerobot.detectLine() != LandjeRobot::LINE::NONE) {
    
        // wacht 30 milliseconden (0,03 seconde)
        delay(30);
    
        // Als beide reflectie sensors een lijn detecteren
        if (landjerobot.detectLine() == LandjeRobot::LINE::BOTH) {
          // keer de robot om en wacht
          landjerobot.turn(LandjeRobot::TURN::LEFT,180,true);
        }
    
        // Als de reflectie sensors links een lijn detecteren
        if (landjerobot.detectLine() == LandjeRobot::LINE::LEFT) {
          // Draai 10 graden naar links en wacht
          landjerobot.turn(LandjeRobot::TURN::LEFT,10,true);
        }
    
        // Als de reflectie sensors rechts een lijn detecteren
        if (landjerobot.detectLine() == LandjeRobot::LINE::RIGHT) {
          // Draai 10 graden naar rechts en wacht
          landjerobot.turn(LandjeRobot::TURN::RIGHT,10,true);
        }
    
        // Laat de robot weer verder rijden
        landjerobot.move(LandjeRobot::DIRECTION::FORWARD);
    
      } // einde if
  
    }

### Opdracht 4

```
int mode = 0;

void setup() {

  // "Lees" de stand van de mode schakelaar
  mode = landjerobot.mode();

  // Als schakelaar op "1" staat
  if (mode == 1) {
    // Start met rijden als de robot aangezet wordt en
    // wacht niet
    landjerobot.move(LandjeRobot::DIRECTION::FORWARD);
  }
  
}

void loop() {

  // Als de schakelaar op "1" staat.
  if (mode == 1) {
    // Als er niet niets (!) gedetecteerd wordt door de 
    // reflectie sensors doe dan iets
    if (landjerobot.detectLine() != LandjeRobot::LINE::NONE) {
      
      // wacht 30 milliseconden (0,03 seconde)
      delay(30);
      
      // Als beide reflectie sensors een lijn detecteren
      if (landjerobot.detectLine() == LandjeRobot::LINE::BOTH) {
        // keer de robot om en wacht
        landjerobot.turn(LandjeRobot::TURN::LEFT,180,true);
      }
      
      // Als de reflectie sensors links een lijn detecteren
      if (landjerobot.detectLine() == LandjeRobot::LINE::LEFT) {
        // Draai 10 graden naar links en wacht
        landjerobot.turn(LandjeRobot::TURN::LEFT,10,true);
      }
      
      // Als de reflectie sensors rechts een lijn detecteren
      if (landjerobot.detectLine() == LandjeRobot::LINE::RIGHT) {
        // Draai 10 graden naar rechts en wacht
        landjerobot.turn(LandjeRobot::TURN::RIGHT,10,true);
      }
      
      // Laat de robot weer verder rijden
      landjerobot.move(LandjeRobot::DIRECTION::FORWARD);
      
    } // einde if
  } else { // Als de schakelaar op "2" staat

  }
  
}
```

## Les 10, meer sensoren en motors

### Opdracht 1

```
void setup() {

    landjerobot.look(LandjeRobot::LOOK::FORWARD);
}

void loop() {
    
}
```

```
void setup() {

    landjerobot.look(LandjeRobot::LOOK::FAR_LEFT);
    delay(2000);
    landjerobot.look(LandjeRobot::LOOK::FORWARD);
    delay(2000);
    landjerobot.look(LandjeRobot::LOOK::FAR_RIGHT);

}

void loop() {
    
}
```

### Opdracht 2

```
void setup() {
  
   landjerobot.mouthOpen();
   delay(5000);
   landjerobot.mouthClosed();
   delay(5000);
   
   landjerobot.talk(10);
    
}
```

### Opdracht 3

Geluid verplaatst zich met een snelheid van 343 meter per seconde. Dus als het 12 seconden duurt voordat je de echt hoort heeft het geluid 343 * 12 of 4116 meter afgelegd. Maar het geluid moet zich verplaatsen naar de berg en weer terug. Daarom is de werkelijke afstand tot de berg 4116 meter gedeeld door 2. De afstand is dus 2058 meter of ongeveer 2km. 

### Opdracht 4

```
void setup() {

    int afstand = 400;
  
    Serial.begin(9600);
    delay(2000);
    
    // druk de gemeten afstand af zolang
    // de afstand groter is dan 5 cm.
    while (afstand > 5) {
      afstand = landjerobot.measureDistance();
      Serial.println(afstand);
    }
    
    // Laat de robot 10 seconden praten
    landjerobot.talk(10);
    
}
```

## Les 11, Een nieuw programma

### Opdracht 1

De oplossing is;

* Als de linker sensor een lijn detecteert, ga dan 10cm terug en draai 45 graden naar rechts. Ga dan verder vooruit.
* Als de rechter sensor een lijn detecteert, ga dan 10cm terug en draai 45 graden naar links. Ga dan verder vooruit.
* Als beide sensors een lijn detecteren, ga dan 10cm terug en draai 180 graden naar links of rechts. Ga dan verder vooruit.

### Opdracht 2

De robot moet vooruit gaan rijden als de mode witch op mode "2" is ingesteld en de robot wordt aangezet. Dus in de functie ```setup()``` moet een instructie toegevoegd worden zodat de robot vooruit gaat rijden.

Dit kan op twee manieren bereikt worden. Als eerste door een if-statement waardoor de robot vooruit gaat rijden als het in mode 2 staat.

```
void setup() {

  // "Lees" de stand van de mode schakelaar
  mode = landjerobot.mode();

  // Als schakelaar op "1" staat
  if (mode == 1) {
    // Start met rijden als de robot aangezet wordt en
    // wacht niet
    landjerobot.move(LandjeRobot::DIRECTION::FORWARD);
  } else {
    // Als schakelaar op "2" staat
    // Start met rijden als de robot aangezet wordt en
    // wacht niet
    landjerobot.move(LandjeRobot::DIRECTION::FORWARD);
  }
  
}
```

Hetzelfde resultaat kan bereikt worden door uit het bestaande programma wat regels te verwijderen. Ongeacht in welke stand de mode schakelaar staat moet de robot vooruit gaan rijden.

```
void setup() {

  // "Lees" de stand van de mode schakelaar
  mode = landjerobot.mode();

  // Start met rijden als de robot aangezet wordt en
  // wacht niet
  landjerobot.move(LandjeRobot::DIRECTION::FORWARD);
  
}
```

### Opdracht 3

Dit is een basis versie van de programma regels om de robot binnen de lijnen te laten blijven rijden.

```
    // Als er niet niets (!) gedetecteerd wordt door de 
    // reflectie sensors doe dan iets
    if (landjerobot.detectLine() != LandjeRobot::LINE::NONE) {
    
      // wacht 30 milliseconden (0,03 seconde)
      delay(30);
    
      if (landjerobot.detectLine() == LandjeRobot::LINE::LEFT) {
        landjerobot.move(LandjeRobot::DIRECTION::BACKWARD, 10, true);
        landjerobot.turn(LandjeRobot::TURN::RIGHT, 45, true);
      }

      if (landjerobot.detectLine() == LandjeRobot::LINE::RIGHT) {
        landjerobot.move(LandjeRobot::DIRECTION::BACKWARD, 10, true);
        landjerobot.turn(LandjeRobot::TURN::LEFT, 45, true);
      }

      if (landjerobot.detectLine() == LandjeRobot::LINE::BOTH) {
        landjerobot.move(LandjeRobot::DIRECTION::BACKWARD, 10, true);
        landjerobot.turn(LandjeRobot::TURN::LEFT, 180, true);
      }
      
      landjerobot.move(LandjeRobot::DIRECTION::FORWARD);
    } // einde if
```

Met de basis versie van de programma regels kan de robot in een eindeloze herhaling blijven hangen. Dezelfde beweging zal dan telkens herhaald worden. Dit kan vooral gebeuren wanneer de robot in een hoek van de lijnen beland. Door wat willekeur toe te voegen wordt dit probleem opgelost. 

```
    // Als er niet niets (!) gedetecteerd wordt door de 
    // reflectie sensors doe dan iets
    if (landjerobot.detectLine() != LandjeRobot::LINE::NONE) {
    
      // wacht 30 milliseconden (0,03 seconde)
      delay(30);
    
      if (landjerobot.detectLine() == LandjeRobot::LINE::LEFT) {
        landjerobot.move(LandjeRobot::DIRECTION::BACKWARD, random(5,10), true);
        landjerobot.turn(LandjeRobot::TURN::RIGHT, random(20,90), true);
      }

      if (landjerobot.detectLine() == LandjeRobot::LINE::RIGHT) {
        landjerobot.move(LandjeRobot::DIRECTION::BACKWARD, random(5,10), true);
        landjerobot.turn(LandjeRobot::TURN::LEFT, random(20,90), true);
      }

      if (landjerobot.detectLine() == LandjeRobot::LINE::BOTH) {
        landjerobot.move(LandjeRobot::DIRECTION::BACKWARD, random(5,10), true);
        landjerobot.turn(LandjeRobot::TURN::LEFT, random(160,200), true);
      }
      
      landjerobot.move(LandjeRobot::DIRECTION::FORWARD);
    } // einde if
```

### Opdracht 4

```
void setup() {

  // "Lees" de stand van de mode schakelaar
  mode = landjerobot.mode();

  // Laat de robot naar voren kijken
  landjerobot.look(LandjeRobot::LOOK::FORWARD);
  
  // Start met rijden als de robot aangezet wordt en
  // wacht niet
  landjerobot.move(LandjeRobot::DIRECTION::FORWARD);
  
}
```

### Opdracht 5

```
    // Meet de afstand
    int afstand = landjerobot.measureDistance();

    // Stop als de afstand minder dan 10 cm is.
    if (afstand < 10) {
      landjerobot.move(LandjeRobot::DIRECTION::STOP);
    }
```

### Opdracht 6

Naar welke richting wil je de robot sturen?; Naar links

Gebaseerd op afstand; De langst gemeten afstand.

```
    // Meet de afstand
    int afstand = landjerobot.measureDistance();

    // Stop als de afstand minder dan 10 cm is.
    if (afstand < 10) {
      landjerobot.move(LandjeRobot::DIRECTION::STOP);
      
      // Meet afstand links van de robot
      landjerobot.look(LandjeRobot::LOOK::LEFT);
      delay(1000);
      int links = landjerobot.measureDistance();

      // Meet afstand rechts van de robot
      landjerobot.look(LandjeRobot::LOOK::RIGHT);
      delay(1000);
      int rechts = landjerobot.measureDistance();
      
      // Kijk weer naar voren
      landjerobot.look(LandjeRobot::LOOK::FORWARD);
      
      if (links > rechts) {
        landjerobot.turn(LandjeRobot::TURN::LEFT, 45, true);
      } else {
        landjerobot.turn(LandjeRobot::TURN::RIGHT, 45, true);
      }
      
      // Rijd weer vooruit
      landjerobot.move(LandjeRobot::DIRECTION::FORWARD);
    } // einde if 
  }
```

#Les 12, verbeteringen

## Opdracht 1

Wanneer de robot moet draaien, ga dan eerst een stukje achteruit om wat ruimte te maken zodat de robot vrij kan draaien.

```
    // Meet de afstand
    int afstand = landjerobot.measureDistance();

    // Stop als de afstand minder dan 10 cm is.
    if (afstand < 10) {
      // Stop met rijden
      landjerobot.move(LandjeRobot::DIRECTION::STOP);
      
      // Meet afstand links van de robot
      landjerobot.look(LandjeRobot::LOOK::LEFT);
      delay(1000);
      int links = landjerobot.measureDistance();

      // Meet afstand rechts van de robot
      landjerobot.look(LandjeRobot::LOOK::RIGHT);
      delay(1000);
      int rechts = landjerobot.measureDistance();
      
      // Kijk weer naar voren
      landjerobot.look(LandjeRobot::LOOK::FORWARD);
      
      // Rij iets achteruit en draai naar links of rechts
      if (links > rechts) {
        landjerobot.move(LandjeRobot::DIRECTION::BACKWARD, 10, true);
        landjerobot.turn(LandjeRobot::TURN::LEFT, 45, true);
      } else {
        landjerobot.move(LandjeRobot::DIRECTION::BACKWARD, 10, true);
        landjerobot.turn(LandjeRobot::TURN::RIGHT, 45, true);
      }
      
      // Rijd weer vooruit
      landjerobot.move(LandjeRobot::DIRECTION::FORWARD);
    } // einde if
  }
```

Of eenvoudiger geprogrammeerd met minder herhaling van programmaregels. Denk aan de DRY regel!

```
    // Meet de afstand
    int afstand = landjerobot.measureDistance();

    // Stop als de afstand minder dan 10 cm is.
    if (afstand < 10) {
      // Stop met rijden
      landjerobot.move(LandjeRobot::DIRECTION::STOP);
      
      // Meet afstand links van de robot
      landjerobot.look(LandjeRobot::LOOK::LEFT);
      delay(1000);
      int links = landjerobot.measureDistance();

      // Meet afstand rechts van de robot
      landjerobot.look(LandjeRobot::LOOK::RIGHT);
      delay(1000);
      int rechts = landjerobot.measureDistance();
      
      // Kijk weer naar voren
      landjerobot.look(LandjeRobot::LOOK::FORWARD);
      
      // Rij iets achteruit
      landjerobot.move(LandjeRobot::DIRECTION::BACKWARD, 10, true);
      
      // Draai naar links of rechts
      if (links > rechts) {
        landjerobot.turn(LandjeRobot::TURN::LEFT, 45, true);
      } else {
        landjerobot.turn(LandjeRobot::TURN::RIGHT, 45, true);
      }
      
      // Rijd weer vooruit
      landjerobot.move(LandjeRobot::DIRECTION::FORWARD);
    } // einde if
  }
```

## Opdracht 2

```
    // Meet de afstand
    int afstand = landjerobot.measureDistance();

    // Stop als de afstand minder dan 10 cm is.
    if (afstand < 10) {
    
      // Stop met rijden
      landjerobot.move(LandjeRobot::DIRECTION::STOP);
   
      // Mopper
      landjerobot.talk(5);
              
      // Meet afstand links van de robot
      landjerobot.look(LandjeRobot::LOOK::LEFT);
      delay(1000);
      int links = landjerobot.measureDistance();

      // Meet afstand rechts van de robot
      landjerobot.look(LandjeRobot::LOOK::RIGHT);
      delay(1000);
      int rechts = landjerobot.measureDistance();
      
      // Kijk weer naar voren
      landjerobot.look(LandjeRobot::LOOK::FORWARD);
      
      // Rij iets achteruit
      landjerobot.move(LandjeRobot::DIRECTION::BACKWARD, 10, true);
      
      // Draai naar links of rechts
      if (links > rechts) {
        landjerobot.turn(LandjeRobot::TURN::LEFT, 45, true);
      } else {
        landjerobot.turn(LandjeRobot::TURN::RIGHT, 45, true);
      }
      
      // Rijd weer vooruit
      landjerobot.move(LandjeRobot::DIRECTION::FORWARD);
    } // einde if
  }
```

## Opdracht 3

```
    // Meet de afstand
    int afstand = landjerobot.measureDistance();

    // Stop als de afstand minder dan 10 cm is.
    if (afstand < 10) {
      
      // Controleer de gemeten afstand
      int totaalafstand = 0;
      for (int x=1; x<=5;x++) {
        totaalafstand = totaalafstand + landjerobot.measureDistance(); 
      }
      
      if (totaalafstand < 50) {
      
        // Stop met rijden
        landjerobot.move(LandjeRobot::DIRECTION::STOP);
        
        // Mopper
        landjerobot.talk(5);
      
        // Meet afstand links van de robot
        landjerobot.look(LandjeRobot::LOOK::LEFT);
        delay(1000);
        int links = landjerobot.measureDistance();
  
        // Meet afstand rechts van de robot
        landjerobot.look(LandjeRobot::LOOK::RIGHT);
        delay(1000);
        int rechts = landjerobot.measureDistance();
        
        // Kijk weer naar voren
        landjerobot.look(LandjeRobot::LOOK::FORWARD);
        
        if (links > rechts) {
          landjerobot.move(LandjeRobot::DIRECTION::BACKWARD, 10, true);
          landjerobot.turn(LandjeRobot::TURN::LEFT, 45, true);
        } else {
          landjerobot.move(LandjeRobot::DIRECTION::BACKWARD, 10, true);
          landjerobot.turn(LandjeRobot::TURN::RIGHT, 45, true);
        }
        
         // Rijd weer vooruit
         landjerobot.move(LandjeRobot::DIRECTION::FORWARD);
      } // einde if
    }

```

# Appendix

## Voorbeeld oplossing

```

#include <LandjeRobot.h>

// Aansluitingen van de robot motors.
const int motor[2][4] = {
  {2, 3, 4, 5}, {6, 7, 8, 9}
} ;

// Aansluitingen van de lijn sensoren
const int lineSensors[2] = { 10, 11 } ;
// Lichte vloer met donker lijnen = true
// Donkere vloer met lichte lijnen = false 
const bool lineSensorInverse = true ;

// Omtrek van de wielen in cm
const int wheelRadiusMM = 21 ;
// Afstand tussen de wielen in cm
const int trackWidthMM = 98 ;

// Aansluiting van de ultrasoon sensor
int ultraPin = 13 ;

// Aansluiting van de servo
int servoPin = 14 ;

// Aansluiting van het led 
int mouthledPin = 15 ;

// Aansluiting van de mode schakelaar
int switchPin = 0 ;

LandjeRobot landjerobot(motor, LandjeRobotMotorController::STEPMODE::FULL_STEP, wheelRadiusMM , trackWidthMM, lineSensors, lineSensorInverse, ultraPin, servoPin, mouthledPin, switchPin) ;

int mode = 0;

void setup() {

  // "Lees" de stand van de mode schakelaar
  mode = landjerobot.mode();

  // Laat de robot naar voren kijken
  landjerobot.look(LandjeRobot::LOOK::FORWARD);
  
  // Start met rijden als de robot aangezet wordt en
  // wacht niet
  landjerobot.move(LandjeRobot::DIRECTION::FORWARD);
  
}

void loop() {

  // Als de schakelaar op "1" staat.
  if (mode == 1) {
    // Als er niet niets (!) gedetecteerd wordt door de 
    // reflectie sensors doe dan iets
    if (landjerobot.detectLine() != LandjeRobot::LINE::NONE) {
      
      // wacht 30 milliseconden (0,03 seconde)
      delay(30);
      
      // Als beide reflectie sensors een lijn detecteren
      if (landjerobot.detectLine() == LandjeRobot::LINE::BOTH) {
        // keer de robot om en wacht
        landjerobot.turn(LandjeRobot::TURN::LEFT,180,true);
      }
      
      // Als de reflectie sensors links een lijn detecteren
      if (landjerobot.detectLine() == LandjeRobot::LINE::LEFT) {
        // Draai 10 graden naar links en wacht
        landjerobot.turn(LandjeRobot::TURN::LEFT,10,true);
      }
      
      // Als de reflectie sensors rechts een lijn detecteren
      if (landjerobot.detectLine() == LandjeRobot::LINE::RIGHT) {
        // Draai 10 graden naar rechts en wacht
        landjerobot.turn(LandjeRobot::TURN::RIGHT,10,true);
      }
      
      // Laat de robot weer verder rijden
      landjerobot.move(LandjeRobot::DIRECTION::FORWARD);
      
    } // einde if
    
  } else { // Als de schakelaar op "2" staat
  
    // Als er niet niets (!) gedetecteerd wordt door de 
    // reflectie sensors doe dan iets
    if (landjerobot.detectLine() != LandjeRobot::LINE::NONE) {
    
      // wacht 30 milliseconden (0,03 seconde)
      delay(30);
    
      if (landjerobot.detectLine() == LandjeRobot::LINE::LEFT) {
        landjerobot.move(LandjeRobot::DIRECTION::BACKWARD, 10, true);
        landjerobot.turn(LandjeRobot::TURN::RIGHT, 45, true);
      }

      if (landjerobot.detectLine() == LandjeRobot::LINE::RIGHT) {
        landjerobot.move(LandjeRobot::DIRECTION::BACKWARD, 10, true);
        landjerobot.turn(LandjeRobot::TURN::LEFT, 45, true);
      }

      if (landjerobot.detectLine() == LandjeRobot::LINE::BOTH) {
        landjerobot.move(LandjeRobot::DIRECTION::BACKWARD, 10, true);
        landjerobot.turn(LandjeRobot::TURN::LEFT, 180, true);
      }
      
      landjerobot.move(LandjeRobot::DIRECTION::FORWARD);
    } // einde if
  
    // Meet de afstand
    int afstand = landjerobot.measureDistance();

    // Stop als de afstand minder dan 10 cm is.
    if (afstand < 10) {
      
      // Controleer de gemeten afstand
      int totaalafstand = 0;
      for (int x=1; x<=5;x++) {
        totaalafstand = totaalafstand + landjerobot.measureDistance(); 
      }
      
      if (totaalafstand < 50) {
      
        // Stop met rijden
        landjerobot.move(LandjeRobot::DIRECTION::STOP);
        
        // Mopper
        landjerobot.talk(5);
      
        // Meet afstand links van de robot
        landjerobot.look(LandjeRobot::LOOK::LEFT);
        delay(1000);
        int links = landjerobot.measureDistance();
  
        // Meet afstand rechts van de robot
        landjerobot.look(LandjeRobot::LOOK::RIGHT);
        delay(1000);
        int rechts = landjerobot.measureDistance();
        
        // Kijk weer naar voren
        landjerobot.look(LandjeRobot::LOOK::FORWARD);
        
        if (links > rechts) {
          landjerobot.move(LandjeRobot::DIRECTION::BACKWARD, 10, true);
          landjerobot.turn(LandjeRobot::TURN::LEFT, 45, true);
        } else {
          landjerobot.move(LandjeRobot::DIRECTION::BACKWARD, 10, true);
          landjerobot.turn(LandjeRobot::TURN::RIGHT, 45, true);
        }
        
         // Rijd weer vooruit
         landjerobot.move(LandjeRobot::DIRECTION::FORWARD);
      }
    }
  }
}
```

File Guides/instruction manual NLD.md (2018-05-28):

# Landje Robot Instructies

De Landje robot heeft zijn eigen set van opdrachten die je hem kunt geven, een instructie-set.
Met deze instructies kun je de robot eenvoudig besturen.

Elke programma voor een Landje Robot moet beginnen met de volgende instructies. Deze instructies hoef je niet te begrijpen.

```
#include <LandjeRobot.h>

// Aansluitingen van de robot.
const int motor[2][4] = {
  {2, 3, 4, 5}, {6, 7, 8, 9}
} ;

// Aansluitingen van de lijn sensoren
const int lineSensors[2] = { 10, 11 } ;
const bool lineSensorInverse = false ;

// Omtrek van de wielen in cm
const int wheelRadiusMM = 21 ;
// Afstand tussen de wielen in cm
const int trackWidthMM = 55 ;

// Aansluiting van de ultrasoon sensor
// Ultrasoon sensor meet de afstand
int ultraPin = 13 ;

// Aansluiting van de servo
// De servo motor beweegt het hoofd van links naar rechts
int servoPin = 14 ;

// Aansluiting van het led 
// Lampje in de mond van de robot
int mouthledPin = 15 ;

// Aansluiting van de mode schakelaar
int switchPin = 0 ;

LandjeRobot landjerobot(motor, LandjeRobotMotorController::STEPMODE::FULL_STEP, wheelRadiusMM , trackWidthMM, lineSensors, lineSensorInverse, ultraPin, servoPin, mouthledPin, switchPin) ;
```

Deze instructies moeten voor de functie *setup()* in het programma geplaatst worden. Knip en plak deze instructies voor aan ieder programma dat je voor de robot schrijft.

## De instructie set             

De Landje robot heeft verschillende eigen instructies. Je hebt instructies om te bewegen, te draaien of bijvoorbeeld om de afstand te meten. Deze instructies geeft je aan de Landje Robot die deze instructies dan weer opvolgd. In het eerste gedeelte van het programma zie je als laatste regel staan. 

`LandjeRobot landjerobot(motor, LandjeRobotMotorController::STEPMODE::FULL_STEP, wheelRadiusMM ,
trackWidthMM, lineSensors, lineSensorInverse, ultraPin, servoPin,mouthledPin) ;`

Met deze lange instructie wordt de robot ingesteld. Na het uitvoeren van deze regel kun je de variabele `landjerobot`. Door middel van deze variabele kun je de instructies aan de robot geven. Je geeft een instructie door aan de variabele `landjerobot` de instructie te plakken. Je plakt een instructie aan landjerobot door middel van een punt. Bijvoorbeeld;   

`landjerobot.talk(5) ;` 

Het plakken van een instructie heet een instructie *geven*. Als er dus ergens staat '*geef de instructie move*' programmeer je dus `landjerobot.move()'. In de volgende paragraaf staan alle speciale instructies die de Landje robot begrijpt. 

### De Landje robot instructieset

De Landje robot heeft verschillende instructies. Bij sommige instructies kun of moet je iets extra's aan de instructie vertellen. Als je de robot wilt laten bewegen kun je bijvoorbeeld vertellen welke richting hij moet op rijden. Het iets extra's vertellen aan een instructie noemen we *doorgeven*. Je *geeft* dus aan de instructie `move` *door* welke richting hij op moet rijden.

`landjerobot.move(LandjeRobot::DIRECTION::FORWARD) ; `

Met `LandjeRobot::DIRECTION::FORWARD` geeft je aan de landjerobot door dat hij vooruit moet bewegen. Het engelse woord `FORWARD` betekent vooruit, `DIRECTION` betekent richting. Je vertelt `LandjeRobot` robot dus dat hij in de `DIRECTION` `FORWARD` moet bewegen. Je zult in andere instructies zien dat de robot kan draaien (`TURN`) naar links (`LEFT`) en rechts (`RIGHT`) of kan kijken (`LOOK`). 

Wat je aan de robot doorgeeft heet *parameter*. Aan elke instructie kan geen, één of meerdere parameters worden doorgegeven. Hoeveel en welke parameters je kan doorgeven verschilt per instructie.

Bij sommige instructies mag je sommige parameters opgegeven, maar hoeft dit niet. Als je de instructie `move` opgeeft mag je de parameter *wachten* opgeven, maar het hoeft niet. Je mag dus de instructie `landerobot.move(LandjeRobot::DIRECTION::FORWARD,10)` geven maar ook `landerobot.move(LandjeRobot::DIRECTION::FORWARD)`. Bij de eerste instructie zal de robot 10 centimeter vooruit gaan rijden. Bij de tweede instructie zal de robot net zolang vooruit blijven rijden totdat je de instructie geeft om te stoppen. Als je een parameter niet opgeeft zal een waarde gekozen worden. Deze gekozen waarde noemt men de standaard waarde. Voor de parameter *afstand* is dit oneindig (∞). 

Als je in deze handleiding de parameter voor instructies opzoekt is er één waarde voor een parameter _onderstreept_. Dit is de waarde welke voor de parameter gekozen zal worden als je de parameter niet doorgeeft aan de instructie. Kijk eens bij de instructie *move*, daar staat dat de waarde '∞' onderstreept. Het teken '∞' betekend oneindig. Als je de parameter *afstand* niet opgeeft blijft de robot oneindig doorrijden.

Instructies kunnen ook een waarde teruggeven. Als een instructie een waarde teruggeeft staat dit bij de instructie vermeld. De instructie *doIMove* heeft geen parameters, maar geeft wel een waarde terug. Als de robot beweegt krijg je *true*, anders *false*.
   
### Instructies

#### move

**Omschrijving**

Laat de robot in een richting bewegen

**Syntax**

move( richting ) ;   
move( richting , afstand) ;   
move( richting , afstand, wachten) ;

**Parameters**

|Parameter|Type|Waarden|Opmerkingen|
|:---|:---|:---|:---|
| richting | | LandjeRobot::DIRECTION::STOP </br>LandjeRobot::DIRECTION::FORWARD</br>LandjeRobot::DIRECTION::BACKWARD | |
| afstand |int| 0.._∞_| De afstand die bewogen moet worden in centimeters |
| wachten |bool| true</br>_false_ | Wacht (true) met het uitvoeren van de volgende instructie totdat de opgegeven afstand is afgelegd |

**Geeft terug**

niets

**Voorbeeld**

```
// beweeg de robot vooruit
landjerobot.beweeg(LandjeRobot::DIRECTION::FORWARD) ;

// beweeg de robot 10cm achteruit
landjerobot.beweeg(LandjeRobot::DIRECTION::BACKWARD,10) ;

// beweeg de robot 20cm vooruit en wacht 
// totdat de opgegeven afstand is afgelegd
landjerobot.beweeg(LandjeRobot::DIRECTION::FORWARD,20,true) ;

```

#### doIMove

**Omschrijving**

Geeft aan of de robot beweegt.

**Syntax**

doIMove() ;   

**Parameters**

geen
        
**Geeft terug**

|Type|Waarde|Opmerkingen|
|:---|:---|:---|
|bool| true | Deze waarde wordt teruggegeven als de robot aan het bewegen is |
|bool| false | Als de robot niet beweegt wordt deze waarde teruggeveven |

**Voorbeeld**

```
// beweeg de robot vooruit
landjerobot.move(LandjeRobot::DIRECTION::FORWARD) ;

if (doIMove()) {
    Serial.println("Ik beweeg!") ;
}

```

#### turn

**Omschrijving**

Laat de robot in een bepaalde richting draaien 

**Syntax**

turn( richting ) ;   
turn( richting , hoek) ;   
turn( richting , hoek, wachten) ;

**Parameters**

|Parameter|Type|Waarden|Opmerkingen|
|:---|:---|:---|:---|
| richting | | LandjeRobot::TURN::STRAIGHT</br>LandjeRobot::TURN::LEFT</br>LandjeRobot::TURN::RIGHT | De draairichting van de robot. De waarde STRAIGHT laat de robot weer recht voor- of achteruit rijden |
| hoek |int| 0..360 </br>_90_| Het aantal graden dat de robot moet draaien. Een hoek van 90 graden is een rechte hoek |
| wachten |bool| true</br>_false_ | Wacht (true) met het uitvoeren van de volgende instructie totdat de opgegeven afstand is afgelegd |

**Draairichtingen van de robot**

        
**Geeft terug**

niets

**Voorbeeld**

```
// draai de robot naar links
landjerobot.draai(LandjeRobot::TURN::LEFT) ;

// laat de robot een rondje rechtsom draaien
landjerobot.draai(LandjeRobot::TURN::RIGHT,360) ;

```

#### look

**Omschrijving**

Laat de robot in een richting kijken

**Syntax**

look( richting ) ;   

**Parameters**

|Parameter|Type|Waarden|Opmerkingen|
|:---|:---|:---|:---|
| richting | | LandjeRobot::LOOK::FORWARD</br>LandjeRobot::LOOK::LEFT</br>LandjeRobot::LOOK::RIGHT</br>LandjeRobot::LOOK::FAR\_LEFT</br>LandjeRobot::LOOK::FAR\_RIGHT | |

**Kijkrichtingen van de robot**


**Geeft terug**

niets

**Voorbeeld**

```
// Kijk naar links
landjerobot.look(LandjeRobot::LOOK::LEFT) ;
```

#### talk

**Omschrijving**

Laat de robot 'praten' door een lichtje in de mond te laten knipperen.

**Syntax**

talk( duur ) ;   

**Parameters**

|Parameter|Type|Waarden|Opmerkingen|
|:---|:---|:---|:---|
| duur | int | 0..∞ | Aantal seconden dat de robot 'praat'|

**Geeft terug**

niets

**Voorbeeld**

```
// Praat 7 seconden
landjerobot.talk(7);
```

#### doITalk

**Omschrijving**

Geeft aan of de robot aan het praten is.

**Syntax**

doITalk() ;   

**Parameters**

geen
        
**Geeft terug**

|Type|Waarde|Opmerkingen|
|:---|:---|:---|
|bool| true | Deze waarde wordt teruggegeven als de robot aan het praten is |
|bool| false | Als de robot niet praat wordt deze waarde teruggeveven |

**Voorbeeld**

```
// Laat de robot praten
landjerobot.talk(60) ;

if (doITalk()) {
    Serial.println("Ik praat!") ;
}

```

#### mouthClosed

**Omschrijving**

Laat de robot zijn mond 'dicht' doen door het led-je uit te zetten

**Syntax**

mouthClosed() ;   

**Parameters**

geen
        
**Geeft terug**

niets

**Voorbeeld**

```
// Laat de robot zijn mond dicht doen
landjerobot.mouthClosed();
```

#### mouthOpen

**Omschrijving**

Laat de robot zijn mond 'open' doen door het led-je aan te zetten

**Syntax**

mouthOpen() ;   

**Parameters**

geen
        
**Geeft terug**

niets

**Voorbeeld**

```
// Laat de robot zijn mond open doen
landjerobot.mouthOpen();
```

#### measureDistance

**Omschrijving**

Meet de afstand van de robot tot een ander object

**Syntax**

measureDistance() ;   

**Parameters**

geen
        
**Geeft terug**

|Type|Waarde|Opmerkingen|
|:---|:---|:---|
|int| 2..400 | Afstand in centimeters |

**Voorbeeld**

```
int gemetenAfstand = 0 ;
// Meet de afstand van de robot tot een ander object
gemetenAfstand  = landjerobot.measureDistance() ;

Serial.print("Gemeten afstand ") ;
Serial.print(gemetenAfstand) ;
Serial.println(" cm") ;

```

#### detectLine

**Omschrijving**

Geeft aan of er een lijn wordt gedetecteerd

**Syntax**

detectLine() ;   

**Parameters**

geen
        
**Geeft terug**

|Type|Waarde|Opmerkingen|
|:---|:---|:---|
|| LandjeRobot::LINE::NONE</br>LandjeRobot::LINE::LEFT</br> LandjeRobot::LINE::RIGHT</br> LandjeRobot::LINE::BOTH | NONE geeft aan dat er geen lijn gedetecteerd wordt. Bij BOTH wordt zowel links als rechts een lijn gedetecteerd |

**Voorbeeld**

```

(
if (detecteerLijn() != LandjeRobot::LINE::NONE) {
    Serial.println("Er is een lijn gedetecteerd") ;
}

```

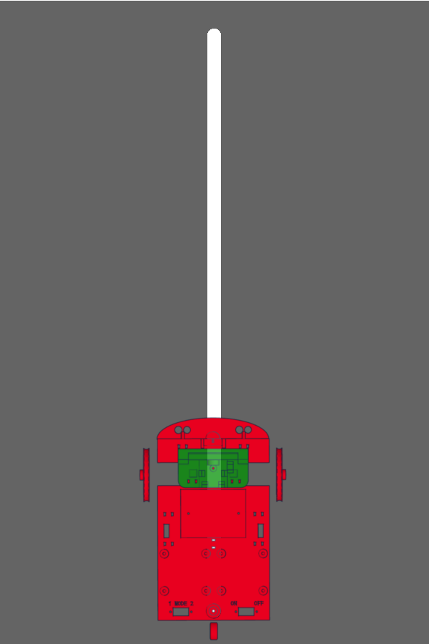
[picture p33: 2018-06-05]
docs/Student guide/Lesson_9_LineFollow_1.png

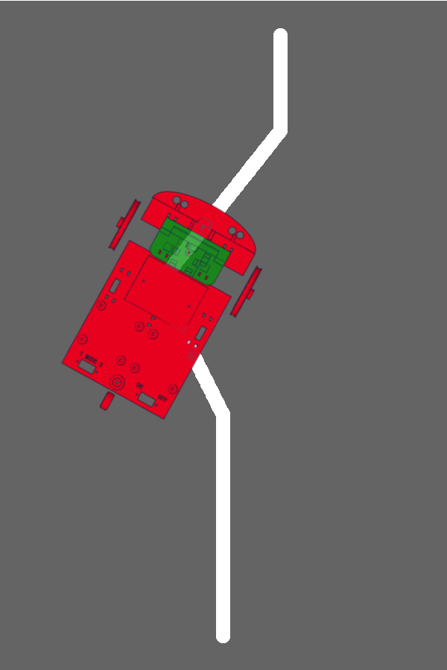
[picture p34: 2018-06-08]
docs/Student guide/Lesson_9_LineFollow_6.png

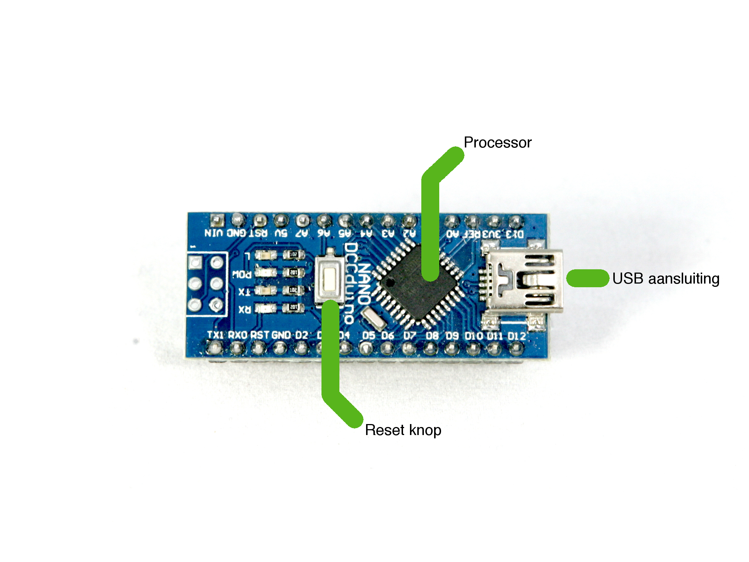
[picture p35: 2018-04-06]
docs/Student guide/Lesson1_Arduino.png

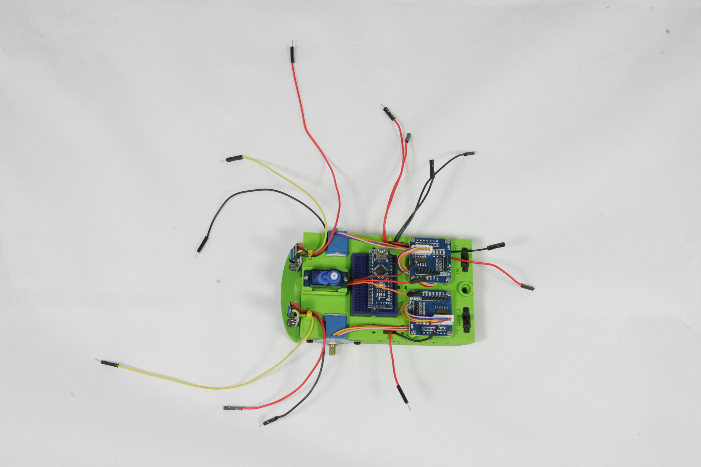
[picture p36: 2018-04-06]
docs/Student guide/Lesson2_FrameWired.JPG

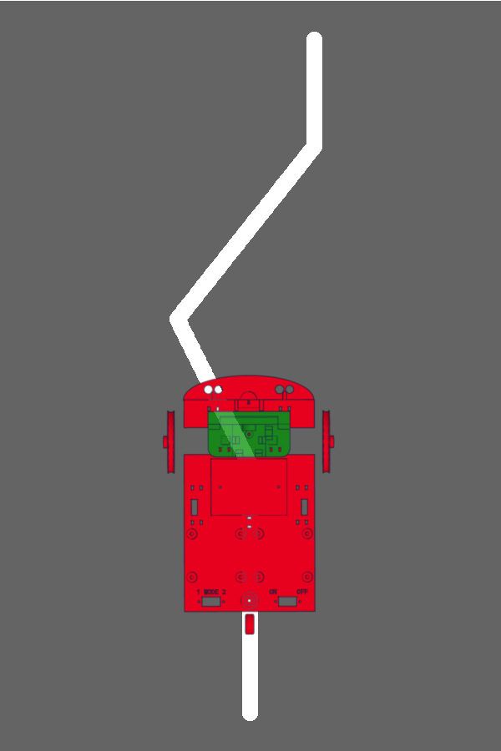
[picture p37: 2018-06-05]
docs/Student guide/Lesson_9_LineFollow_3.png

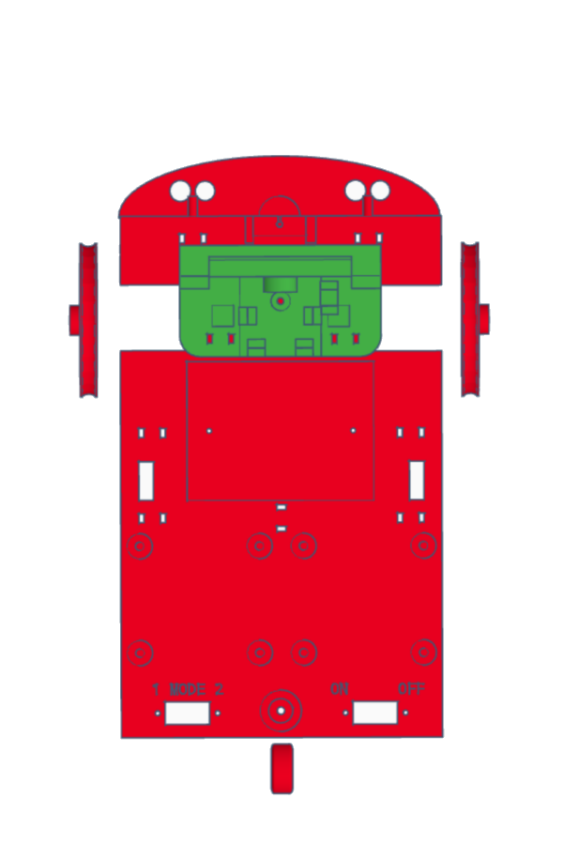
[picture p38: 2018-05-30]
docs/Student guide/Lesson_8_Robot.png

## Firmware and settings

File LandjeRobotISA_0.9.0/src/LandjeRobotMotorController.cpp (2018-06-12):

/*
  LandjeRobotMotorController.cpp - Part of the library "LandjeRobot"

  This file is part of the Reddipped.com Landje robot library.

  This work is licensed under the Creative Commons
  Attribution-NonCommercial-ShareAlike 4.0 International License.
  To view a copy of this license, visit
  http://creativecommons.org/licenses/by-nc-sa/4.0/.

  Created by Peter van Nes, October 16, 2017.
  Check Github latest release @ https://github.com/reddipped/LandjeRobot

 */

#include "Arduino.h"
#include "LandjeRobotMotorController.h"

LandjeRobotMotorController::LandjeRobotMotorController(int motor_data[][4], LandjeRobotMotorController::STEPMODE stepperMode, int wheelRadiusMM, int trackWidthMM)
{

    _stepCount = 0;
    _stepperMode = stepperMode;
    _wheelCircumferenceMM = 2 * PI * wheelRadiusMM;
    _turnRadiusCircumferenceMM = PI * trackWidthMM;

    // Convert pin numbers to pinbit mask, set input/output mode,
    // store the output port register per pin
    for (int m = 0; m <= 1; m++)
    {
        for (int n = 0; n <= 3; n++)
        {
            _motorPinBitmaskData[m][n] = digitalPinToBitMask(motor_data[m][n]);                  // translate pin number to port register bitmask for selected pin.
            *portModeRegister(digitalPinToPort(motor_data[m][n])) |= _motorPinBitmaskData[m][n]; // Set pin to output in DDR register
            _motorRegisterData[m][n] = portOutputRegister(digitalPinToPort(motor_data[m][n]));   // Get the output port register for selected pin.

            *_motorRegisterData[m][n] &= ~_motorPinBitmaskData[m][n]; // LOW
        }
    }
}

boolean LandjeRobotMotorController::isMoving()
{
    return ((_moveDirection != LandjeRobotMotorController::DIRECTION::STOP) ||
            (_turnDirection != LandjeRobotMotorController::TURN::STRAIGHT));
}

LandjeRobotMotorController::SetDirection(LandjeRobotMotorController::DIRECTION newMoveDirection)
{
    _moveDirection = newMoveDirection;
    // No specified distance
    _stepCount = 0;
}

LandjeRobotMotorController::SetDirection(LandjeRobotMotorController::DIRECTION newMoveDirection, int cm)
{
    _stepCount = (cm * 10) / (_wheelCircumferenceMM / (_stepsPerRotation / (int)_stepperMode));
    _moveDirection = newMoveDirection;
}

LandjeRobotMotorController::SetTurn(LandjeRobotMotorController::TURN newTurnDirection)
{
    SetTurn(newTurnDirection, 90);
}

LandjeRobotMotorController::SetTurn(LandjeRobotMotorController::TURN newTurnDirection, int degrees)
{
    SetDirection(LandjeRobotMotorController::DIRECTION::STOP);
    _stepCount = ((_turnRadiusCircumferenceMM / 360) * degrees) / (_wheelCircumferenceMM / (_stepsPerRotation / (int)_stepperMode));
    _turnDirection = newTurnDirection;
}

LandjeRobotMotorController::Move()
{

    // Execute same step for all motors
    for (int m = 0; m <= 1; m++)
    {

        // Move one step
        switch (_moveDirection)
        {
        // forward
        case DIRECTION::FORWARD:
            _motorStep[m] = _motorStep[m] + ((int)_stepperMode * (int)_motorDirection[m]);
            break;
        // backward
        case DIRECTION::BACKWARD:
            _motorStep[m] = _motorStep[m] - ((int)_stepperMode * (int)_motorDirection[m]);
            break;
        }

        // Turn one step
        switch (_turnDirection)
        {
        // left
        case TURN::LEFT:
            _motorStep[m] = _motorStep[m] - ((int)_stepperMode * (m == 0 ? (int)_motorDirection[m] : (int)-_motorDirection[m]));
            break;
        // right
        case TURN::RIGHT:
            _motorStep[m] = _motorStep[m] + ((int)_stepperMode * (m == 0 ? (int)_motorDirection[m] : (int)-_motorDirection[m]));
            break;
        }

        // if step is past last, begin at first step
        if (_motorStep[m] > 7)
        {
            _motorStep[m] = 0 + ((int)_stepperMode - 1);
        }

        // if step is behind first, begin at last step
        if (_motorStep[m] < 0)
        {
            _motorStep[m] = 7;
        }
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

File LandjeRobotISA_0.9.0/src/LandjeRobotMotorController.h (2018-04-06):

/*
  LandjeRobotMotorController.h - Part of the library "LandjeRobot"

  This file is part of the Reddipped.com Landje robot library.

  This work is licensed under the Creative Commons
  Attribution-NonCommercial-ShareAlike 4.0 International License.
  To view a copy of this license, visit
  http://creativecommons.org/licenses/by-nc-sa/4.0/.

  Created by Peter van Nes, October 16, 2017.
  Check Github latest release @ https://github.com/reddipped/LandjeRobot

 */

#ifndef LandjeRobotMotorController_h
#define LandjeRobotMotorController_h

#include <Arduino.h>

class LandjeRobotMotorController
{

  public:
    // Set to a value of >0 if a limited number of steps need to be made
    int _stepCount;

  // Symbolic names for DIRECTION of travel
    enum class DIRECTION {
        STOP = 0,    // Stop
        FORWARD = 1, // Move forward
        BACKWARD = 2 // Move backward
    } ;

    // Symbolic names for DIRECTION of rotation
     enum class TURN {
        STRAIGHT = 0, // Right on
        LEFT = 1,     // TURN left
        RIGHT = 2     // TURN right
    } ;

    // Stepper motor 28BYJ-48
    // 1 for half step 63.684 steps per rotation = 4076
    // 2 for full step 4076/2                    = 2038
    // Symbolic name for half or full step mode
    enum class STEPMODE {

        HALF_STEP = 1,
        FULL_STEP = 2
    } ;

    LandjeRobotMotorController(int motor_data[2][4], LandjeRobotMotorController::STEPMODE, int, int);
    SetDirection(LandjeRobotMotorController::DIRECTION);
    SetDirection(LandjeRobotMotorController::DIRECTION, int);
    SetTurn(LandjeRobotMotorController::TURN);
    SetTurn(LandjeRobotMotorController::TURN, int);
    bool isMoving();
    Move();

    boolean moving = false;

  private:
    // Steps per full rotation for 28BYJ-48 stepper motor in half step mode
    const int _stepsPerRotation = 4076;

    // Default step mode
    LandjeRobotMotorController::STEPMODE _stepperMode;

    // Wheel radius and calculated circumference
    float _wheelCircumferenceMM;
    float _turnRadiusCircumferenceMM;

    // Default direction
    LandjeRobotMotorController::DIRECTION _moveDirection = LandjeRobotMotorController::DIRECTION::STOP;
    LandjeRobotMotorController::TURN _turnDirection = LandjeRobotMotorController::TURN::STRAIGHT;

    // Store current motor position
    int _motorStep[2] = {0, 0};

    // Sets default forward direction per motor
    const int _motorDirection[2] = {1, -1};

    // Store bitmask for motor pins
    int _motorPinBitmaskData[2][4] = {{0, 0, 0, 0}, {0, 0, 0, 0}};

    // Store output registers for motor pins
    volatile uint8_t *_motorRegisterData[2][4];
};

#endif

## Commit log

2018-04-06 re initialized after corruption
    [robot frame.stl, robot head.stl, robot screw organizer.stl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]
2018-04-09 Stepper motor rewiring done
2018-05-28 Library and doc update
    More or les finished debugging section
    Updatef/formatted library code
    Setup instruction set chapter
2018-05-30 Code fixes and more instructions
    * Corrected trackwidth
    [LandjeRobotMotorController.cpp]
2018-06-08 Fixed turn direction motors
    [LandjeRobotMotorController.cpp]
2018-06-11 new updates
    * added som sections to chapter 9
    * added generic arduino instructions to instructionset
    * minor styling additions
    * added solutions for new assignments
2018-06-12 fixed line detection and turn direction issue
    [LandjeRobotMotorController.cpp]
2018-09-21 hopefully fixed corrupt checkin
    fingers crossed
2018-09-22 3d Model
    Model updated
    [Landje Robot.stl, robot frame.stl, robot head.stl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]
